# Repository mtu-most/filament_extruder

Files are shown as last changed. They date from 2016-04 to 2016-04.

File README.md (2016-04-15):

<h1>MOST Filament Extruder V4.1</h1>

The MOST filament extruder for making your own filament.

<a href="https://github.com/mtu-most/most-scad-libraries">MOST SCAD libraries</a> are required if the SCAD files are used. Put all SCAD files in the same directory. The renderer provides a relatively easy way to render the parts while still allowing the extruder library to be used in other designs.

Models of all the printed parts are available in the models/stl directory and pictures of the printed parts may be found in models/rendering.

Development of the electronics was done with Kicad and all source is available in the aptly named kicad directory. Gerbers are there, too.

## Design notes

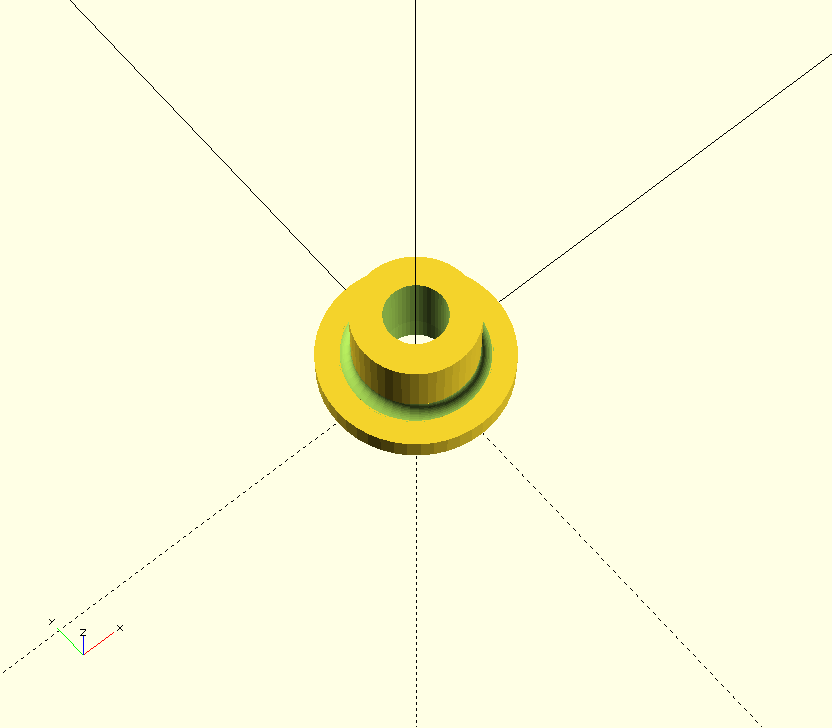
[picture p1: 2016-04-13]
models/rendering/bearing_bushing.png

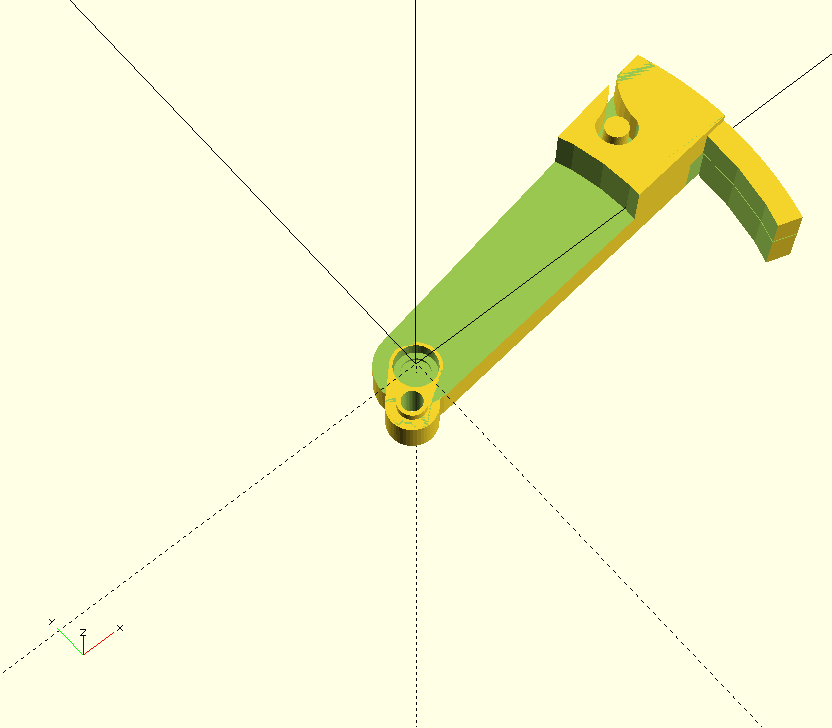
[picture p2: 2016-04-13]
models/rendering/qc_diameter.png

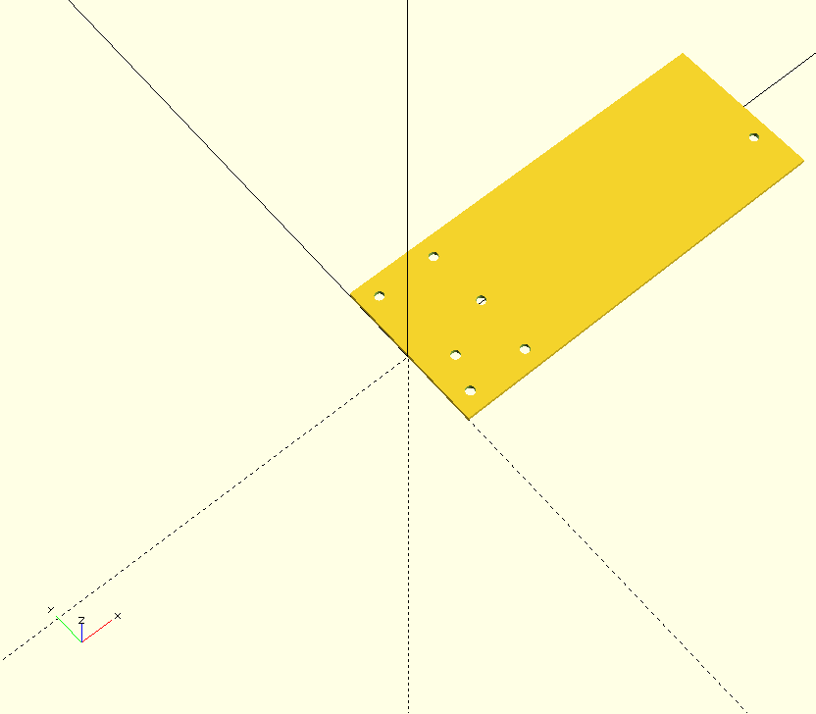
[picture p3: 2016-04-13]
models/rendering/qc_mount-template.png

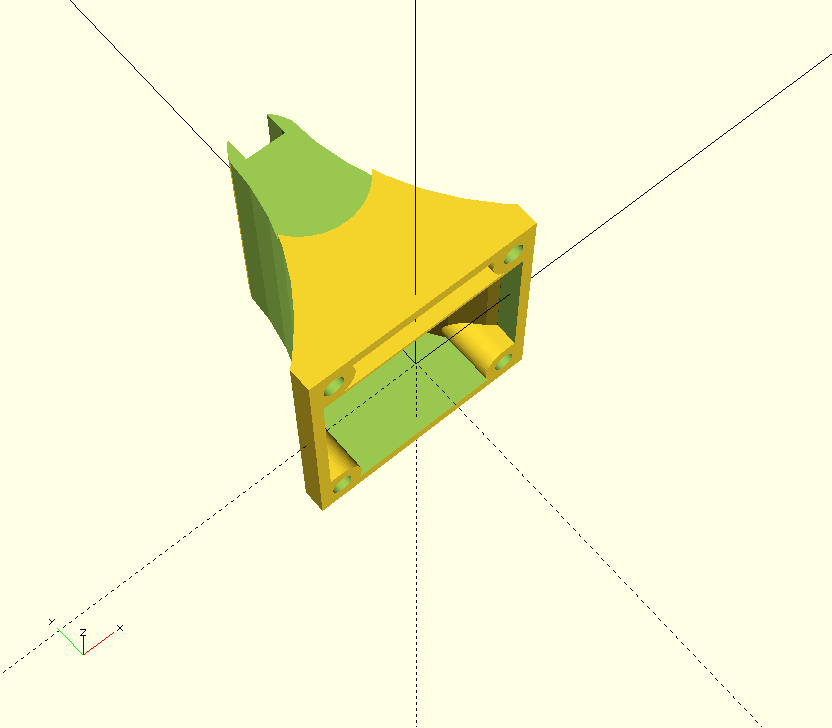
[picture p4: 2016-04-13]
models/rendering/fan_shroud.png

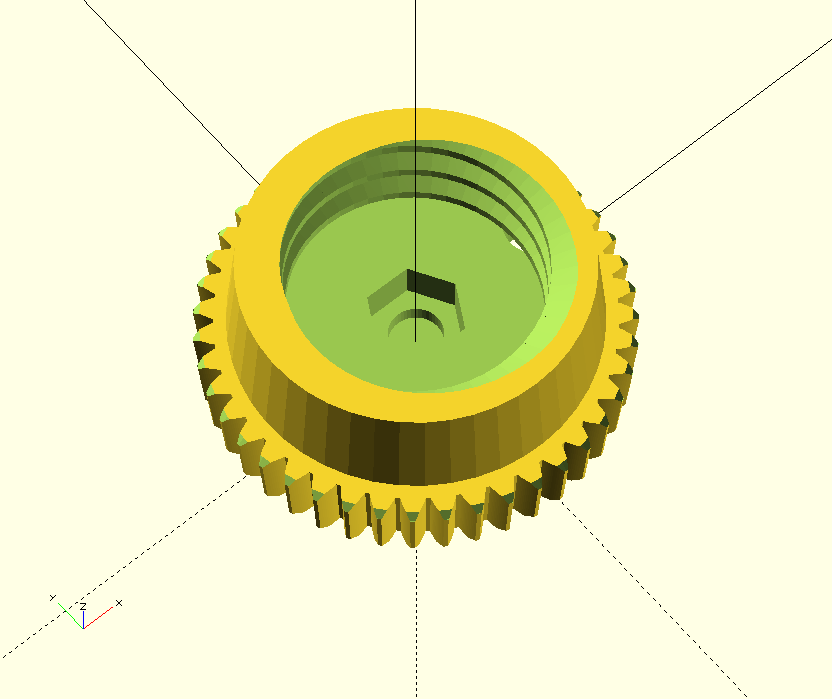
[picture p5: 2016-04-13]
models/rendering/gear_large.png

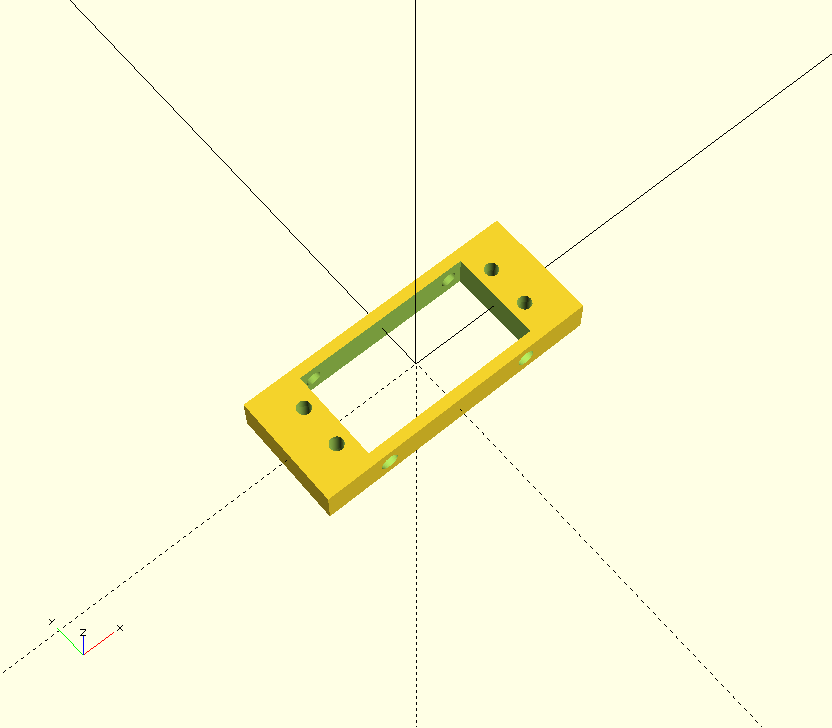
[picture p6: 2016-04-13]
models/rendering/servo_mount.png

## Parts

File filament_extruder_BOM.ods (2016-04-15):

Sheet: Extruder
Filament extruder Bill of Materials
Extruder
Part | Length | Count | Functional group | Description |  | Note | Example
1-5/8” slotted hole strut channel | 24” | 2 | Extruder | Frame base |  |  | http://www.mcmaster.com/#3310t475/=wjtfif
1-1/2” x 2-1/2” x 1/4” angle | 4” | 3 | Extruder | Motor and extruder brackets |  |  | http://www.mcmaster.com/#9017k79/=wjtg2r
5/8” ship auger, 17-18” long |  | 1 | Extruder | Extruder auger |  |  | http://www.mcmaster.com/#2818a12/=wjudd1
1/2” npt brass medium pressure cap with 1.5-2mm hole |  | 1 | Extruder | Extruder nozzle |  |  | http://www.mcmaster.com/#50785k164/=wjug3t
1/4” - 20 threaded rod | 3” | 4 | Extruder | Fixing floor flanges to brackets |  |  | http://www.mcmaster.com/#98841a029/=wjun2h
1/4” - 20 threaded rod | 9” | 2 | Extruder | Fixing all three floor flanges together |  |  | hardware store
1/2” npt black iron floor flange |  | 3 | Extruder | Thermal and torque breaks |  |  | http://www.amazon.com/LDR-310-F-12-Flange-2-Inch/dp/B000FPASJ8
1/2” npt nipple, threaded both ends | 6” | 2 | Extruder | Extruder barrel, feed barrel |  |  | http://www.mcmaster.com/#44615k484/=wjulv6
1/4” - 20 nuts |  | 20 | Extruder | various |  |  | http://www.mcmaster.com/#90473a029/=wjuout
1/4” washers |  | 24 | Extruder | various |  |  | http://www.mcmaster.com/#92141a029/=wjuplf
¼' – 20 7/8” OD fender washers |  | 4 | Extruder | Thrust bearing retainers |  |  | http://www.mcmaster.com/#91090a107/=wjur3k
1” wheel bearing |  | 1 | Extruder | Thrust bearing |  | Bearing block may need to be modified depending on OD or outer race | http://www.amazon.com/Martin-Wheel-BK-1-Bearing-Repair/dp/B00C1ZQT6G?s=automotive
Kapton tape |  |  | Extruder | Fixing nichrome to barrel
1/2” fiberglass pipe insulation | 5” | 1 | Extruder | Hot end insulator |  |  | http://www.mcmaster.com/#5556k31/=ww86uo
Printed bearing block |  | 1 | Extruder | Thrust bearing block
Printed feed chute front |  | 1 | Extruder | Feed chute
Printed feed chute back |  | 1 | Extruder | Feed chute
M3 x 16mm socket head cap screw |  | 4 | Extruder | Feed chute
1/4” - 20 strut channel nut |  | 6 | Extruder | Fixing angle brackets to strut |  |  | http://www.mcmaster.com/#3259t31/=z2wsyp
1/4” - 20 strut channel nut |  | 2 | Extruder | Fixing hanger bracket to strut |  |  | http://www.mcmaster.com/#3259t31/=z2wsyp
Hanger bracket |  | 1 | Extruder | Hanging extruder |  | manufactured
4cm x 4cm 1 1cm 24VDC fan |  | 1 | Extruder | Cooling fan
Printed fan mount |  | 1 | Extruder | Cooling fan mount
M3 x 35mm socket head cap screw |  | 4 | Extruder | Cooling fan mount
M3 hex nut |  | 4 | Extruder | Cooling fan mount
Printed cooling fan shroud |  | 1 | Extruder | Cooling fan mount
3mm id x 6mm OD PTFE tubing | 18” | 1 | Extruder | Filament guide sheathing
AC-powered version
22 rpm AC gear motor, 110V w/speed control, bracket and mounting screws |  | 1 | Extruder | Extruder drive motor |  |  | http://www.amazon.com/21rpm-Factory-Motor-Controller-Bracket/dp/B00G34C37A?s=lamps-light
15mm rigid shaft coupling w/ keyway |  | 1 | Extruder | Gearbox-auger coupling |  |  | http://www.mcmaster.com/#5395t512/=wjtj2m
7/16” deep socket, 1/4” drive |  | 1 | Extruder | Gearbox-auger coupling |  |  | http://www.mcmaster.com/#5543a76/=wjucze
31AWG glass insulated Nichrome wire, 8 ohm/ft | 17' | 1 | Extruder | Extruder barrel heating element |  |  | https://ultimachine.com/content/31-awg-nichrome-wire-0 | 31AWG glass insulated Nichrome wire, 8 ohm/ft | 31AWG glass insulated Nichrome wire, 8 ohm/ft | 17 | 1 | Extruder barrel heating element | https://ultimachine.com/content/31-awg-nichrome-wire-0 | 31AWG glass insulated Nichrome wire, 8 ohm/ft | 17 | 1 | Extruder barrel heating element | https://ultimachine.com/content/31-awg-nichrome-wire-0 | 31AWG glass insulated Nichrome wire, 8 ohm/ft | 17 | 1 | Extruder barrel heating element | https://ultimachine.com/content/31-awg-nichrome-wire-0 | 31AWG glass insulated Nichrome wire, 8 ohm/ft | 17 | 1 | Extruder barrel heating element | https://ultimachine.com/content/31-awg-nichrome-wire-0 | 31AWG glass insulated Nichrome wire, 8 ohm/ft | 17 | 1 | Extruder barrel heating element | https://ultimachine.com/content/31-awg-nichrome-wire-0 | 31AWG glass insulated Nichrome wire, 8 ohm/ft | 17 | 1
24V, 1A power supply |  | 1 | Extruder | Controller and winder power
DC-powered version
20-25rpm, 120W 24VDC gear motor |  | 1 | Extruder | Extruder drive motor |  |  | http://www.aliexpress.com/item/5D120GN-C-DC-Permanent-Magnet-Reducer-Gear-Motor-Big-Power-Reverse-Motor-120W-12V-24V/32283520834.html
12mm rigid shaft coupling w/ keyway one side bored to 13mm |  | 1 | Extruder | Gearbox-auger coupling |  |  | http://www.mcmaster.com/#5395t412/=ww8e8e
31AWG glass insulated Nichrome wire, 8 ohm/ft | 3' | 4 | Extruder | Extruder barrel heating element |  | Four lengths total with pairs in parallel and alternating polarity. Total ~96W. | https://ultimachine.com/content/31-awg-nichrome-wire-0
24V, >=5A power supply |  | 1 | Extruder | System power
Controller
LCD w/ I2C communication |  | 1 | Controller | Interface
8 step rotary encoder with switch |  | 1 | Controller | Interface
Printed interface mount |  | 1 | Controller | Interface
MOST Extruder Controller Board |  | 1 | Controller | Controller
Printed controller board mount |  | 1 | Controller | Controller
Printed knob for encoder |  | 1 | Controller | Controller
Four conductor ribbon cable with 4 pin housings each end | 12” | 1 | Controller | LCD wire
3 ea 28ga stranded, insulated wire, 3 pin housing one end | 12” | 1 | Controller | Encoder wire
100k-ohm, radial lead NTP thermistor |  | 1 | Controller | Extruder barrel temp sensor |  |  | http://www.amazon.com/MAX6675-Module-Thermocouple-Sensor-Arduino/dp/B00MPEUVSK?s=industrial
1” hose clamp |  | 1 | Controller | Affixing thermistor to nozzle
Drop Position Sensor
MOST drop position sensor board |  | 1 | Drop position sensor | Drop position sensor
Printed drop position sensor mount |  | 1 | Drop position sensor | Drop position sensor
6-conductor ribbon cable with keyed pin housings each end | 24” | 1 | Drop position sensor | Communication cable to controller
3mm red LED |  | 1 | Drop position sensor | Illuminator
2 ea 28ga stranded, insulated wire, 2 pin housing one end | 8” | 1 | Drop position sensor | LED power wire
Diffuser (matte finish Scotch tape) |  | 1 | Drop position sensor | Drop position sensor
Winder
24V, 24rpm gear motor |  | 1 | Filament winder | Winder drive motor
Printed large gear/spool cone |  | 1 | Filament winder | Winder drive
Printed spool retainer screw |  | 1 | Filament winder | Secure spool to winder
608zz bearing |  | 2 | Filament winder | Winder bearings
M8 x 40mm hex head cap screw |  | 1 | Filament winder | Winder shaft
8mm flat washer |  | 1 | Filament winder | Winder shaft
M8 nylock nut |  | 1 | Filament winder | Winder shaft
Printed spool winder bearing flange |  | 2 | Filament winder | Winder shaft
1/8” x 2” aluminum strap | 6” | 1 | Filament winder | Winder motor mount
Printed small gear |  | 1 | Filament winder | Winder drive
M3 x 8 set screw |  | 1 | Filament winder | Small gear set screw
M3 x 10 socket head cap screw |  | 2 | Filament winder | Secure winder motor mount to frame
3MM flat washer |  | 2 | Filament winder | Secure winder motor mount to frame
Hall effect switch |  | 1 | Filament winder | Winder rotation detector
Cylindrical magnet |  | 1 | Filament winder | Winder rotation detector
Servo |  | 1 | Filament winder | Winder positioner
Printed filament positioner arm |  | 1 | Filament winder | Winder positioner
Printed servo mount |  | 1 | Filament winder | Winder positioner
M3 x 30 countersunk socket screw |  | 2 | Filament winder | Winder positioner mounting
M3 hex nut |  | 4 | Filament winder | Winder positioner mounting
M3 x 10 socket head cap screw |  | 4 | Filament winder | Servo mounting
M3 hex nut |  | 4 | Filament winder | Servo mounting
3mm flat washer |  | 4 | Filament winder | Servo mounting
3mm id x 6mm OD PTFE tubing | 1/4” | 1 | Filament winder | Low friction filament path for positioner
Diameter and length measurement
1/8” x 2” aluminum strap | 7” | 1 | Length & Diameter | Mounting bracket
Printed diameter lever |  | 1 | Diameter Measurement | Diameter measurement
MR105zz bearing |  | 6 | Diameter Measurement | 2 Lever bearings, 4 filament gauge bearings
M5 x 16 socket head cap screw |  | 1 | Diameter Measurement | lever gauge bearing shaft
M5 x 40 fully threaded socket head cap screw |  | 1 | Diameter Measurement | Idler gauge bearing shaft
M5 x 20 socket head cap screw |  | 1 | Diameter Measurement | Diameter lever pivot shaft
5mm flat washer x 8mm od |  | 1 | Diameter Measurement | Washer on mount side of diameter lever pivot | Produced by chucking an M5 screw with a 5mm washer and nut on it in a drill and turning down with a file.
GT2 belt | 12” | 1 | Diameter Measurement | Diameter measurement pulley engagement
16 tooth GT2 pulley bored to 6.4mm |  | 1 | Diameter Measurement | Diameter measurement pulley engagement
Bourns PDB241-GTR02-104BO linear taper, low friction potentiometer |  | 1 | Diameter Measurement | Signal producing device for diameter measurement
M3 grub screw |  | 1 | Diameter Measurement | Affixing GT2 pulley to pot
Weight |  | 1 | Diameter Measurement | Belt tensioner
Printed filament guide |  | 1 | Diameter Measurement | Guides filament through diameter measurement device
M5 hex nut |  | 1 | Diameter Measurement | Idler bearing shaft nut
Printed length measurement device mount |  | 1 | Length Measurement
Printed length measurement rotor |  | 1 | Length Measurement
Cylinder magnet |  | 1 | Length Measurement
M5 x 20 hex head cap screw |  | 1 | Length Measurement | Rotor shaft
mk7 filament drive gear and set screw |  | 1 | Length Measurement
5mm flat washer |  | 2-4 | Length Measurement | Shims for drive gear
625zz bearing |  | 2 | Length Measurement | Rotor shaft bearings
Hall effect switch |  | 1 | Length Measurement | Rotation detector

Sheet: Winder
Part | Length | Count | Description | Note | Example
Servo |  | 1 | Filament winder guide |  | https://www.adafruit.com/products/155
FilaWinder electronics kit |  | 1 | Controller, sensor, cable | This needs to be replaced with something better | http://www.filastruder.com/products/filawinder
Momentary contact push button switch |  | 3 | Controller interface
5k-ohm potentiomer |  | 1 | Controller interface
SPST rocker switch |  | 2 | Controller interface
2 pin headers |  | 6
3 pin headers |  | 2
Female crimp ends
2” x 1/8” aluminum strip | 6” | 1 | Spool winder mount
608zz bearing |  | 2 | Spool winder shaft
M8 hex head cap screw | 30mm | 1 | Spool winder shaft
M8 nut |  | 1 | Spool winder shaft
Printed bearing blocks |  | 2 | Spool winder shaft
Printed spool gear (large) |  | 1 | Spool winder drive
Printed small gear |  | 1 | Spool winder drive
M3 nut |  | 1 | Set screw for small gear
M3 x 6mm set screw |  | 1 | Set screw for small gear
M3 x 6mm socket head cap screw |  | 1 | Spool winder drive motor mount
6mm diameter Nd magnet |  | 1 | Spool winder rotation detector
Printed filament guide arm |  | 1 | Spacing coil on spool
M3 x 12mm socket head cap screw |  | 2 | Filament guide servo mount
M3 washer |  | 2 | Filament guide servo mount
Printed servo mount |  | 1 | Filament guide servo mount
M3 x 25mm flat-head socket cap screw |  | 2 | Filament guide servo mount
M3 nut |  | 2 | Filament guide servo mount
M3 washer |  | 2 | Filament guide servo mount
Printed control panel |  | 1 | For interface
Printed sensor mount |  | 1 | Filament drop sensor
Printed sensor shroud |  | 1 | Filament drop sensor
Printed fan mount |  | 1 | Filament cooling
Printed fan shroud |  | 1 | Filament cooling
40mm box fan |  | 1 | Filament cooling
1/4” - 20 threaded rod | 36” | 2 | Sensor and fan mounting
1/4” - 20 nut |  | 8 | Sensor and fan mounting
1/4” washer |  | 4 | Sensor and fan mounting
Printed threaded rod mounts |  | 2 | Sensor and fan mounting
1/2” - 13 nut |  | 2 | Sensor and fan mounting
1/2” washer |  | 2 | Sensor and fan mounting
PTFE tubing | 10mm | 1 | Fan filament guide
M3 x 25mm socket head cap screws |  | 4 | Fan mount
M3 nut |  | 4 | Fan mount
M3 washer |  | 4 | Fan mount
LED |  | 1 | Filament drop sensor
Linear sensor array |  | 1 | Filament drop sensor |  | http://www.digikey.com/product-detail/en/TSL1406R/TSL1406-R-ND/3095064
Linear sensor PCB |  | 1 | Filament drop sensor | custom
Printed control board mount |  | 1
M3 x 10mm socket head cap screw |  | 2 | Control board mount
M3 x 6mm socket head cap screw |  | 2 | Control board mount
M3 x 10mm socket head cap screw |  | 2 | Spool winder mount
M3 washer |  | 2 | Spool winder mount
Connection wire |  |  | Various
AC-powered version
12VDC 30 rpm gear motor |  | 1 | Spool winder drive |  | http://www.aliexpress.com/item/24V-6mm-Diameter-Shaft-2-Pins-Terminal-30RPM-Gearbox-DC-Gear-Motor/32238311086.html
DC-powered version
24VDC 30 rpm gear motor |  | 1 | Spool winder drive |  | http://www.aliexpress.com/item/JL-37B3540-216-2430-Electric-Replacing-DC24V-30RPM-DC-Gear-Motor/32323787933.html

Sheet: QC
Part | Length | Count | Description | Note | Example
2” x 1/8” aluminum strip | 7” | 1 | Mount
Low torque potentiometer |  | 1 | Diameter measurement
Rotary encoder |  | 1 | Length measurement
M5 x 25mm hex head cap screw |  | 1 | Idler roller shaft
M5 nut |  | 3 | Idler roller shaft
M5 nut |  | 1 | Pressor roller
MR105zz ball bearing |  | 2 | Pressor and idler rollers
MR105zz ball bearing |  | 2 | Lever bearings
M5 X 20mm socket head cap screw |  | 1 | Lever shaft
M5 nut |  | 1 | Lever shaft
16 tooth GT2 pulley w/ set screw |  | 1 | Diameter measurement
GT2 belt | 40cm | 1 | Diameter measurement
Printed encoder mount |  | 1
Printed lever |  | 1
Printed filament guide |  | 1
PTFE tubing | 25mm | 1 | Diameter-to-length
PTFE tubing | 10mm | 1 | Diameter outlet
PTFE tubing | 40mm | 1 | Length inlet
Connection wire |  |  | Various
2 x 16 LCD panel |  | 1 | Interface
LCD I2C backpack |  | 1 | Interface | Required since insufficient number of pins available on Arduino

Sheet: electronics
Function | Count | Spec/Similar | Price
Controller | 1 | AVR (version?)
Heater power switching | 1 | high power FET (STM STP55NF06) | 1.11
Spool winder motor power switching | 1 | low power FET (STM STP55NF06) | 1.11
Rotary encoder with switch | 1 | (Bourns PEC12R-4120F-S0012) | 1.21
1602 LCD Panel w/ I2C adapter | 1 | (see aliexpress.com) | 1.96
Length measurement | 1 | 400 step low torque rotary encoder (see aliexpress.com) | 12.19
Diameter measurement | 1 | low torque linear taper potentiometer (Bourns series....)
Spool winder motor | 1 | 24V DC gearmotor (see aliexpress.com) | 15.33
Spool rotation sensor | 1 | Hall effect sensor (Optek OH090U) | 1.67
Auger rotation sensor | 1 | Hall effect sensor (Optek OH090U) | 1.67
Drop sensor | 1 | Linear sensor array, TSL1406R (see mouser.com) | 23.93
Drop sensor illumination | 1 | LED, red (see any) | 0.2
Drop sensor controller | 1 | ATTINY45-20XUR (see digikey.com) | 1.42
Hot end temperature sensor | 1 | AD8495 (see digikey.com) | 4.81
Hot end temperature thermocouple | 1 | Type k thermocouple (see amazon.com) | 1.15
Main controller board | 1 | Custom
Drop sensor board | 1 | Custom
Thermocouple amplifier board | 1 | Custom
Not electronic:
Spool rotation sensor magnet | 1 | 3/16” X 1/4” Nd magnet (see K&J magnetics) | 0.38
Auger rotation sensor magnet | 1 | 3/16” X 1/4” Nd magnet (see K&J magnetics) | 0.38
Diameter measurement sensor pulley | 1 | 16 tooth GT2 pulley (see robotdigg.com) | 1.8
Diameter measurement idler bearing | 1 | MR105zz (see robotdigg.com) | 0.6
Diameter measurement idler flanged bearing | 1 | MF105zz (see amazon.com) | 1.19
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

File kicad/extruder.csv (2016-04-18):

Id | Designator | Package | Quantity | Designation | Supplier and ref
1 | C1,C2 | C_0805 | 2 | C22pF
2 | R3,R2,R1 | R_0603 | 3 | R100k
3 | Y1 | Crystal_HC49-SD_SMD | 1 | Crystal
4 | cpu1 | TQFP-32_7x7mm_Pitch0.8mm | 1 | ATMEGA328P-A
5 | ctemp1 | c_elec_3x5.3 | 1 | CP10uF
6 | P1 | Pin_Header_Straight_1x02 | 1 | therm
7 | P2 | Pin_Header_Straight_1x04 | 1 | lcd
8 | P4 | Pin_Header_Straight_1x04 | 1 | qc
9 | P5 | Pin_Header_Straight_1x06 | 1 | ftdi
10 | P6 | Pin_Header_Straight_1x03 | 1 | servo
11 | P7 | Pin_Header_Straight_1x03 | 1 | hall
12 | P11 | Pin_Header_Straight_1x04 | 1 | enc
13 | P12 | Pin_Header_Straight_2x03 | 1 | icsp
14 | Q1,Q2,Q3 | TO-252-2Lead | 3 | IRLR2905PBF
15 | rtemp1 | R_1206 | 1 | R4.7k
16 | P8 | 2Screw | 1 | htr
17 | P13 | 2Screw | 1 | pwr
18 | P14 | Pin_Header_Straight_2x03 | 1 | 24V
19 | P15 | Pin_Header_Straight_2x03 | 1 | 5V
20 | PSU1 | 7-28V | 1 | DC-DC_Buck
21 | D1,D2,D3 | DO-214AC | 3 | D
22 | P9 | Pin_Header_Straight_1x02 | 1 | winder
23 | P10 | 2Screw | 1 | auger
24 | P3,P16,P17,P18 | 1pin | 4 | CONN_01X01
25 | W1,W3,W4 | Pin_Header_Straight_1x01 | 3 | TEST_1P

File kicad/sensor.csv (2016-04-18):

Id | Designator | Package | Quantity | Designation | Supplier and ref
1 | RV1 | Potentiometer_Trimmer-Bourne_TC33-X2 | 1 | POT
2 | O1 | TSL1406R | 1 | TSL1406R
3 | IC1 | SOIJ-8_5.3x5.3mm_Pitch1.27mm | 1 | ATTINY45-S
4 | P1 | Pin_Header_Angled_2x03 | 1 | ICSP
5 | P2 | Pin_Header_Angled_1x02 | 1 | LED
6 | R1 | R_1206 | 1 | R100

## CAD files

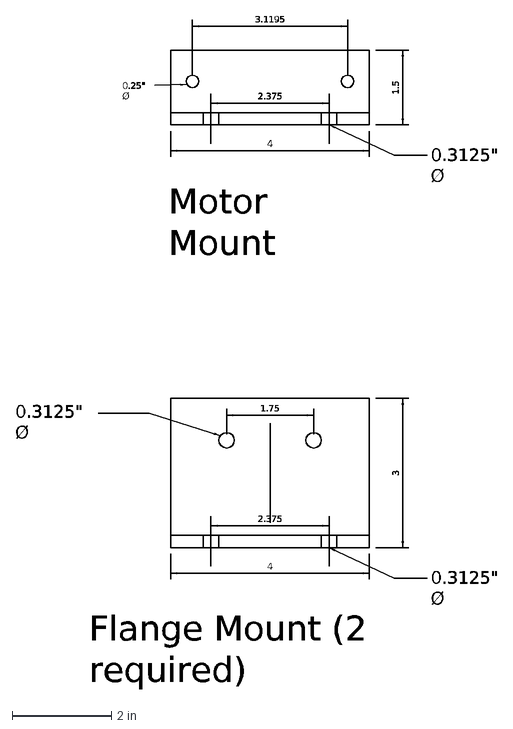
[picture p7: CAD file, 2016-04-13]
cad/motor and flange mounts.dxf
2.375
0.3125" Ø
4
3
1.75
Flange Mount (2 required)
3.1195
0.25" Ø
1.5
Motor Mount

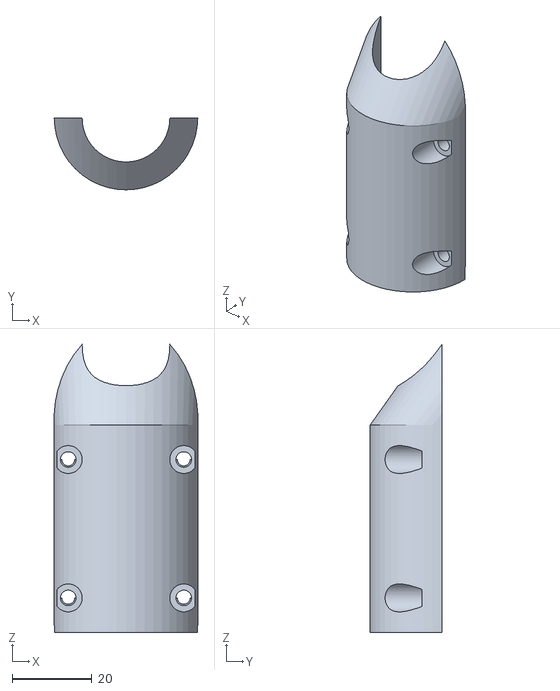
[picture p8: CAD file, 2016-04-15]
models/stl/feed_chute_back.stl
36.1 x 18.0 x 72.3

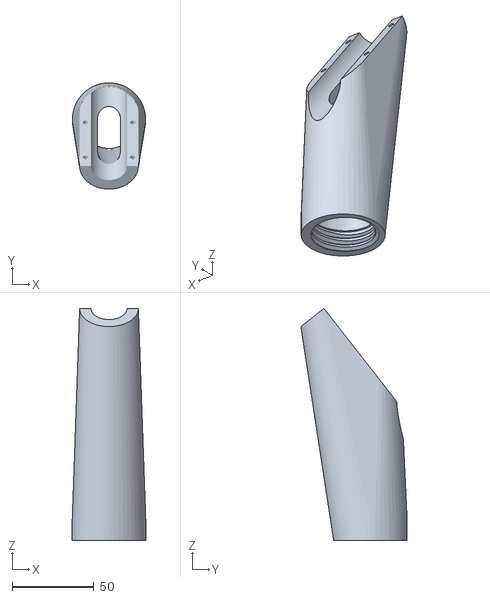
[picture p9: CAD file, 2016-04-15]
models/stl/feed_chute_front.stl
45.0 x 65.1 x 142.0

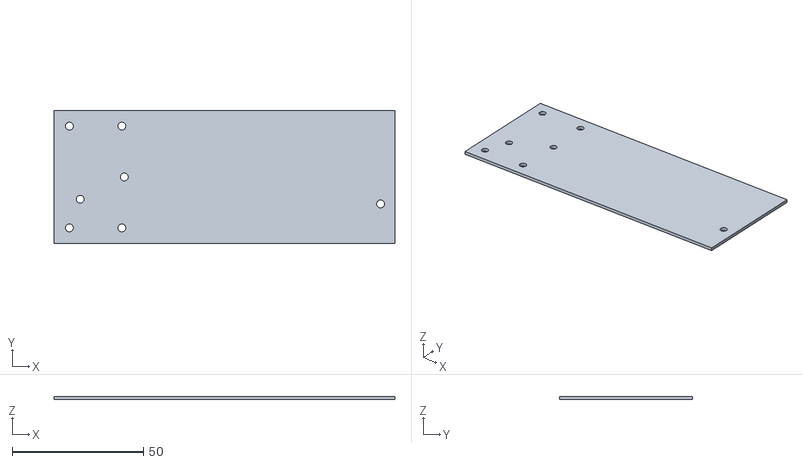
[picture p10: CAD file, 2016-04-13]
models/stl/qc_mount_template.stl
130.0 x 50.8 x 1.33

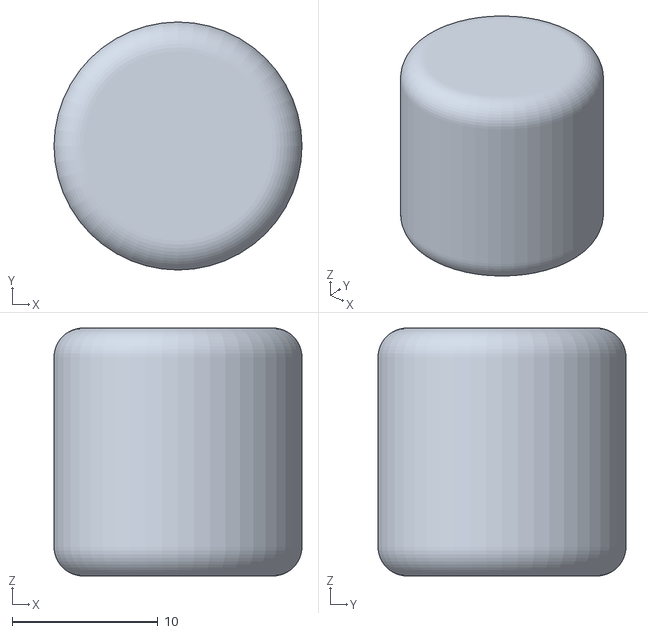
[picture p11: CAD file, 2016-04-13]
models/stl/encoder_knob.stl
17.0 x 17.0 x 17.0

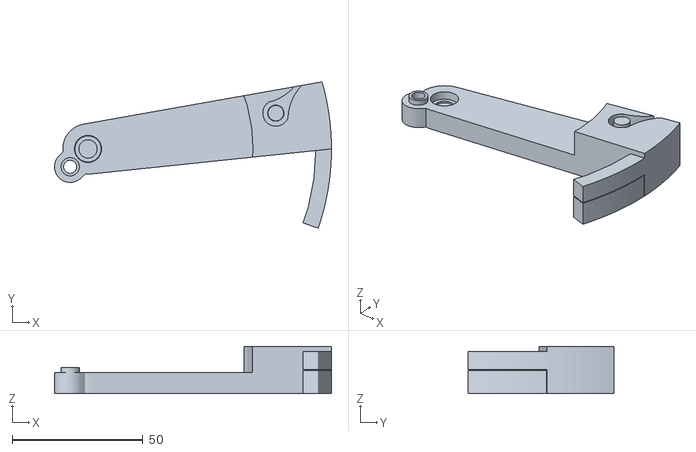
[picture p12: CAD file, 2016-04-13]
models/stl/qc_diameter.stl
105.9 x 56.0 x 18.0

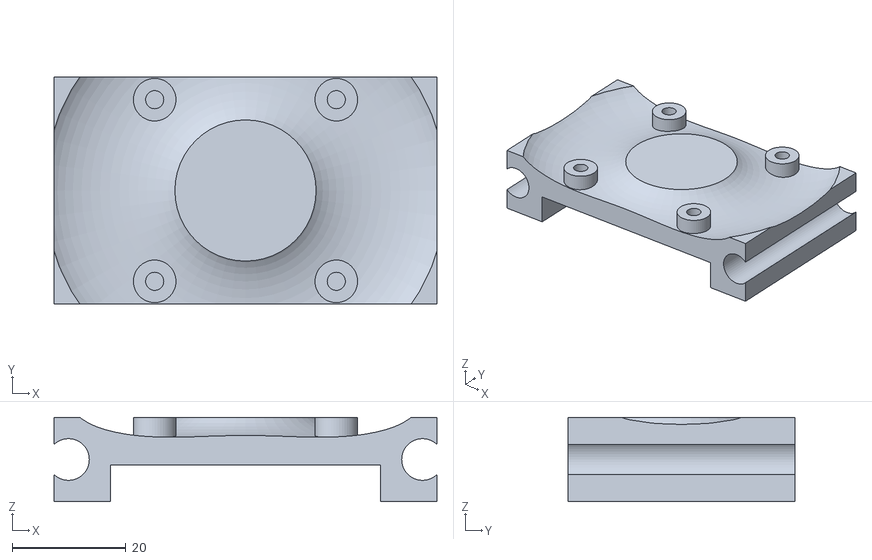
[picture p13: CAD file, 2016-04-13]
models/stl/fan_mount.stl
67.5 x 40.0 x 14.8

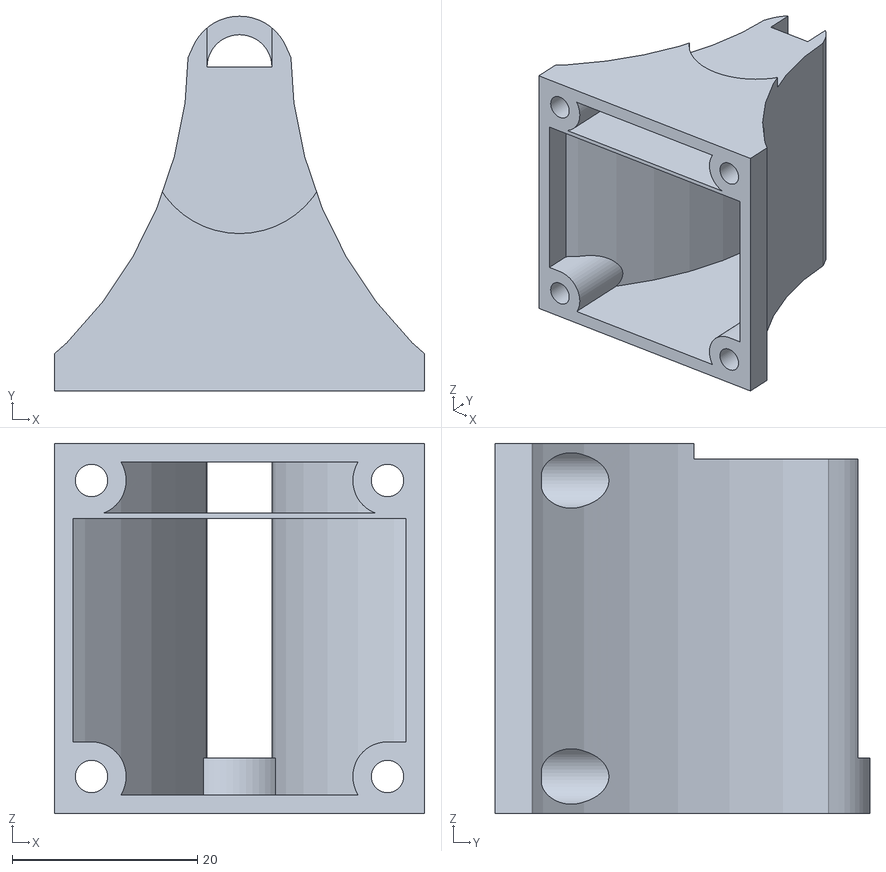
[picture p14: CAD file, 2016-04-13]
models/stl/fan_shroud.stl
40.0 x 40.5 x 40.0

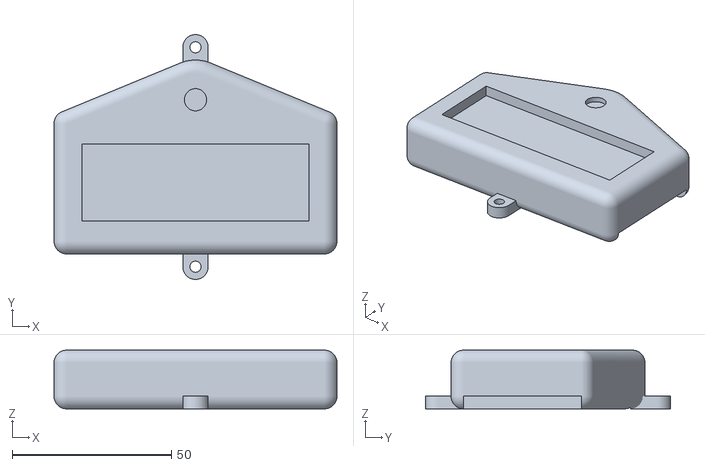
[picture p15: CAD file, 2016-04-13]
models/stl/display_mount.stl
89.0 x 77.0 x 18.5

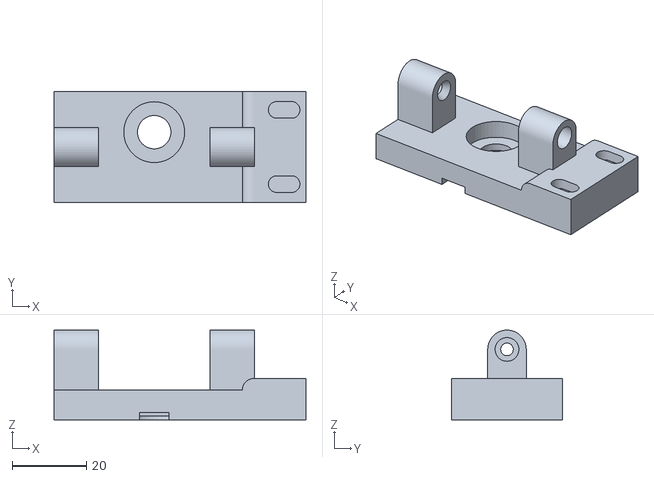
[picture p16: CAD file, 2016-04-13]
models/stl/qc_length.stl
67.9 x 30.0 x 24.2

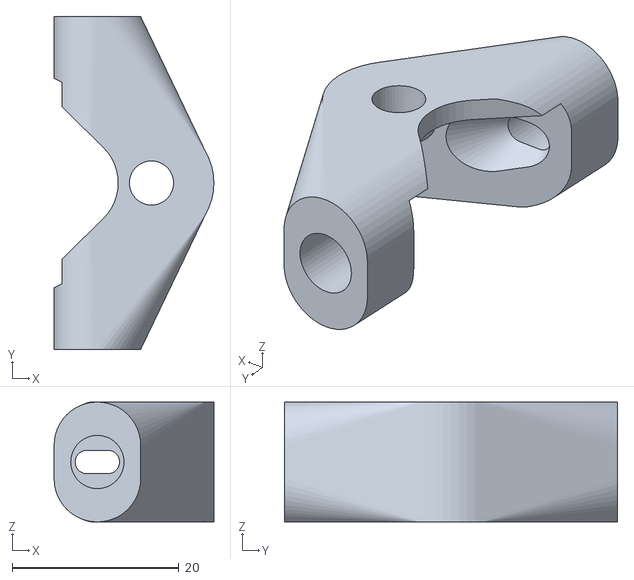
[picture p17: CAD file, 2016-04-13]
models/stl/filament_guide.stl
19.2 x 40.0 x 14.4

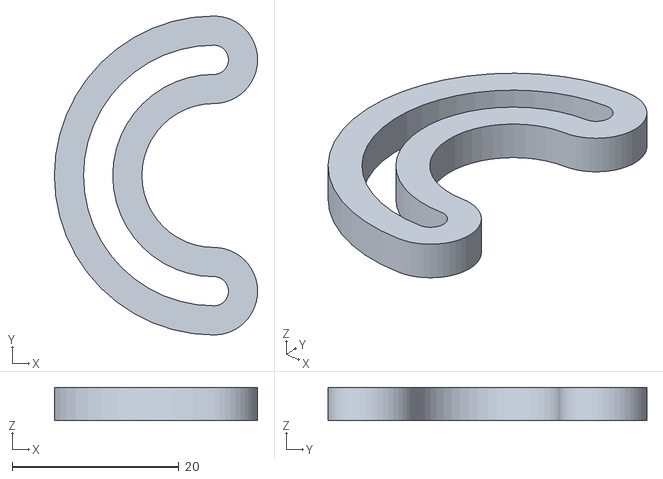
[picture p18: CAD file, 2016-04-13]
models/stl/winder_motor_stay.stl
24.4 x 38.2 x 4.00

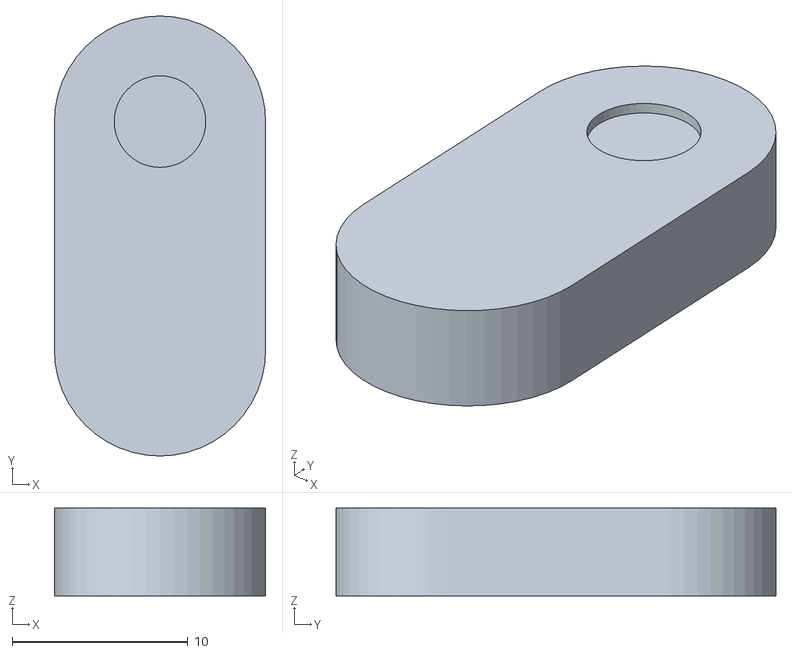
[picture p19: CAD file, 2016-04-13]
models/stl/qc_length_rotor.stl
12.0 x 25.0 x 5.00

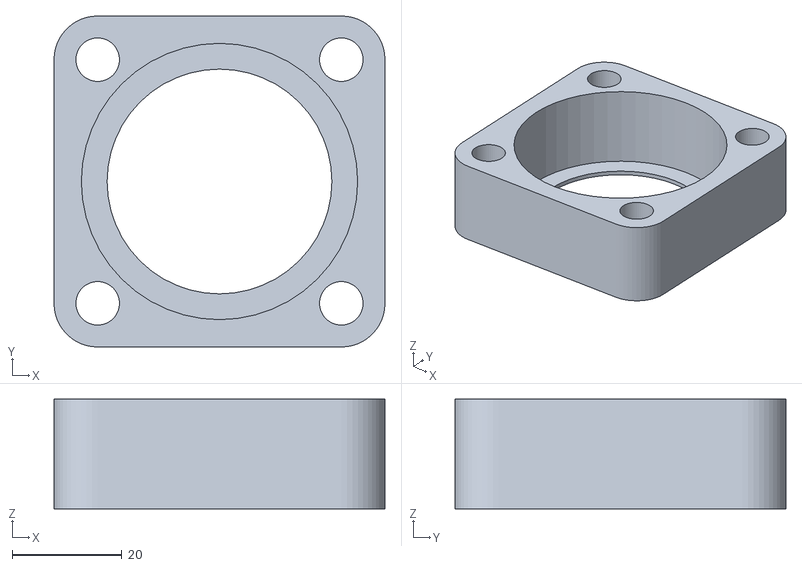
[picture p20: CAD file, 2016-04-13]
models/stl/trailer_bearing_block.stl
60.4 x 60.4 x 20.0

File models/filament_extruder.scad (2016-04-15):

/************************************************************************************

filament_winder.scad - various parts for the winder portion of the MOST filament extruder V10000
Copyright 2015 Jerry Anzalone
Author: Jerry Anzalone <gcanzalo@mtu.edu>

This program is free software: you can redistribute it and/or modify
it under the terms of the GNU Affero General Public License as
published by the Free Software Foundation, either version 3 of the
License, or (at your option) any later version.

This program is distributed in the hope that it will be useful,
but WITHOUT ANY WARRANTY; without even the implied warranty of
MERCHANTABILITY or FITNESS FOR A PARTICULAR PURPOSE. See the
GNU Affero General Public License for more details.

You should have received a copy of the GNU Affero General Public License
along with this program. If not, see <http://www.gnu.org/licenses/>.

************************************************************************************/

include<bearings.scad>
include<fasteners.scad>
include<threads.scad>
include<gear_calculator.scad>
include<parametric_involute_gear_v5.0.scad>

$fn = 48;

layer_height = 0.3;

pi = 3.14159265359;

// extruder parts
od_pipe = 22; // measured 21.52
l_gap = 10;
h_gap = 1.5 * 25.4;
pad_pipe = 7;
od_pipe_engagement = od_pipe + 2 * pad_pipe;
h_pipe_engagement = h_gap + 2 * pad_pipe;
od_hopper_engagement = 24;
l_hopper_base = 70;
w_hopper_base = 25;
t_hopper_walls = 4;
w_clamp = od_pipe_engagement / 2 + 8;
l_clamp = 8;
y_offset_hopper = 45 + od_hopper_engagement / 2;
z_offset_hopper = 80;

cc_flange_mounts = 7 * 25.4 / 4;
d_flange_mounts = 5 * 25.4 / 16;
h_outer_race = 20;
d_outer_race = 50.4;
d_inner = 41;

pitch_hopper = 4.00;
d_hopper = 39; //36.5;
// for the jug adapter:
a_hopper = 38;
pad_threads = 3;
h_threads = 13.1;
id_throat = 30;

h_bushing = 20;
h_bushing_flange = 5;
id_bearing = 25.35;
od_bearing_flange = 39.8;
r_id_bearing = 2.5; // the inner race has a radiused shoulder
d_auger_shank = 12.7;
dmax_auger_shank = 13.25;
h_auger_taper = 6;

// winder motor dims
d_motor_mount_circle = 27.75;
d_motor_mount = 37;
d_shaft_collar = 12;
d_shaft = 6;
d_shaft_flat = 5.3;
l_shaft = 12;
n_mounts = 4;
d_mounts = d_M3_screw;
offset_shaft = 6.81;
t_motor_mount = 4;

// pulleys were originally both 40mm in diameter, changes should be done to both diameters
// to keep belt length the same (unless a different belt is used)
d_pulley_motor = 15;
d_pulley_spool = 65;
d_belt = 4; // belt will be a large o-ring
t_pulley = 6;

id_spool = 52.26;
d_large_cone = id_spool + 2.5;
d_small_cone = id_spool - 2.5;
h_cone = 15;

d_cone_shaft = 8;

d_magnet = 10;// 6.3;
h_magnet = 3;//6.3;

d_c_rod = 5; // using carbon fiber rod for the spool holder since it's available
d_frame_mount = d_M3_screw; // screw diameter mounting dpool holder to frame
offset_frame_mount = 10;
h_frame_mount = offset_frame_mount + d_frame_mount + 3;

bearing_idler = bearing_608;

// servo dims
w_servo = 20;
l_servo = 40.2;
l_servo_flange = 55;
cc_w_servo_mounts = 10;
cc_l_servo_mounts = 48;
d_servo_mounts = d_M3_screw;

d_cable = 7;
d_cable_holder = d_cable + 2;

l_strut_slot = 28; // measure 28.32
d_strut_slot = 14; // measured 14.32
cc_strut_slots = 62.4;

d_sensor_threaded_rod = 25.4 / 4 + 0.5; // diameter of threaded rod holding the sensor and goodies

// light sensor board dims - origin is corner nearest screw terminal
l_sensor_board = 80;
w_sensor_board = 25;
l_sensor = 61.48; // tsl1406r - 61.33
w_sensor = 13.1; // tsl1406r - 12.95
t_sensor = 3.3;
pad_sensor = 3; // sides of sensor surrounded by this much plastic
t_sensor_mount = 10; // the light-facing side of the sensor will have this much plastic over it
cc_sensor_mounts = 2.25 * 25.4;
offset_sensor_centerline = w_sensor / 2 - 5.435;
d_sensor_mounts = 1.75; // 2.3mm diameter openings in sensor
offset_sensor = 25; // distance from axis of threaded rod to center of sensor
l_slot = 43; // 55.5 microns high x 768 pixels = 42.624mm
w_slot = 0.5; // width of the light slot in the sensor mount
l_light_path = 90;

w_sensor_mount = offset_sensor + w_sensor + 6; // width of the sensor mount
l_sensor_mount = l_sensor + 6;

d_light_source = 3; // diameter of the light source
pad_light_source = 3;
t_light_source_mount = 6;
d_light_source_pinhole = 0.5;

// main board dimensions
l_main_board = 71;
w_main_board = 44;
cc_l_mounts = 67 - 3.25;
cc_w_mounts = 39 - 3.25;

d_guide = 4; // ptfe tubing guides

// tensioner loop:
d_loop_tensioner = 135;
d_tensioner = 7;
tensioner_entry_offset = 100;

// quality control device measures diameter and total length of filament
// filament travels through device parallel the x-axis
qc_bearings = bearing_MR105;			// all bearings are the same for simplicity - MR105z keeps the overall sive of the lever down
qc_advantage = 9.65;								// ratio of long:short. Precision increases with increasing advantage.
d_qc_drive_gear = 12.5;						// diamter of the drive gear body
d_qc_drive_gear_hob = 11.3;				// diameter of the hobbed poriton of drive gear
d_qc_encoder_mount = 7; 					// d_M7_screw;
d_qc_pivot = d_M5_screw;
t_qc_lever = 18;									// end thickness of the lever
t_qc_lever_pivot = 8;
qc_pulley_pitch = 2;
qc_pulley_teeth = 16;
qc_pot_mechanical_rotation = 300;	// maximum rotation of potentiometer
qc_max_displacement = 2.5; 				// maximum diameter of the filament to be measured
qc_target_displacement = 1.75; 		// target displacement
a_qc_bearings = 45;								// the idler will be angle about the pivot with respect to the x-axis by this amount

/* it's easier to calculate displacement from angle subtended:
		theta = 1; // angle resulting from displacement
		f = 2 * qc_short * pow(sin(theta / 2), 2); // short leg of triangle
		e = (qc_bearings[0] + d_qc_drive_gear_hob) / 2 + 2 * qc_short * sin(theta / 2) * cos(theta / 2); // long leg of triangle
		D = pow(pow(e, 2) + pow(f, 2), 0.5) - qc_bearings[0]; // displacement happens on the hypotenuse; subtract bearing radii from h to get D

		Doing this in a spreadsheet, plotting a vs D and fitting a line to the area of interest yields
		a good approximation of angle from D, the method used below
*/

// calculation of the total angle subtended can be approximated linearly up to 5 mm diameter by:
d_qc_pulley = qc_pulley_pitch * qc_pulley_teeth / pi / 2;
a_max_qc = (qc_max_displacement - 0.047763) / 0.153332;
a_target_qc = (qc_target_displacement - 0.047763) / 0.153332;
// short side of pivot determined by the diameter of the idler bearing and diameter of pivot
qc_short = (qc_bearings[0] + d_qc_pivot) / 2 + 2;				// add a bit for an M5 nut on the pivot
qc_long = qc_short * qc_advantage;
max_qc_pot_rotation = 360 * a_max_qc * qc_long * pi / 180 / (qc_pulley_pitch * qc_pulley_teeth);
target_qc_pot_rotation = 360 * a_target_qc * qc_long * pi / 180 / (qc_pulley_pitch * qc_pulley_teeth);

// stationary bearings are offset to keep the filament straight when at target displacement:
x_offset_qc_stationary = qc_short * cos(180 - a_qc_bearings) - qc_bearings[0];
y_offset_qc_stationary = -qc_short * (1 - cos(a_qc_bearings - a_target_qc) + sin(a_qc_bearings));

// length measurement instrument
// encoder will sit between two pieces of PTFE tubing so that the filament must bend over the drive gear
l_filament_path = 30;
deflection = 1.9;
od_tubing = 6.4;		// 3mm id x 6mm od PTFE tubing
id_tubing = 3;
pad_tubing = 2;
l_qc_length_base = l_filament_path + 24;
w_qc_length_base = 30;
t_qc_length_base = 8;
z_offset_tubing = 11; // the bearings on the diameter measurement tool are about 11mm off plate face
offset_encoder = d_qc_drive_gear_hob / 2 + qc_target_displacement / 2 - (id_tubing - qc_target_displacement) / 2 - deflection;
cc_qc_length_mounts = w_qc_length_base - 10;
inset_qc_length_mounts = 6;
d_encoder_mount = 6.8;

// for the qc mounting plate
l_qc_mount = ceil(qc_long - x_offset_qc_stationary + 20);
w_qc_mount = 2 * 25.4;	// 2" x 1/8" Al strip
t_qc_mount = 3;

color_bearing = [0.6, 0.6, 0.6];
color_fastener = [0, 0.7, 0];

w_al_strip = 25.4 * 2;
t_al_strip = 25.4 / 8;
spool_drive_cc = 40; // spool drive gear c-c
n_teeth_small = 13;
n_teeth_large = 44;
t_gear = 12;
pitch_spool_threads = 6;
d_spool_threads = d_small_cone - 6;

cp = fit_spur_gears(n1 = n_teeth_small, n2 = n_teeth_large, spacing = spool_drive_cc);
r_spool_magnet_circle = outer_radius(teeth = n_teeth_large, circular_pitch = cp) - d_magnet / 2 - 4;

d_encoder_knob = 17;

d_fan_blade = 38;
d_fan_hub = 25;
h_fan_mount = d_sensor_threaded_rod + 8;
cc_fan_mounts = 32;
d_fan_shroud_outlet = d_tensioner + 4;
offset_fan_entry = 33;
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

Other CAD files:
models/stl/thread_holder.stl
models/stl/gear_small.stl
models/stl/servo_mount.stl
models/stl/bearing_bushing.stl
models/filament_extruder_renderer.scad
models/stl/feed_chute.stl
models/stl/filament_guide_arm.stl
models/stl/gear_large.stl
models/stl/idler_cone.stl
models/stl/sensor_mount.stl
models/stl/spool_drive_bearing_block.stl

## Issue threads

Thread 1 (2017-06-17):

libraries are lacking

Patola, 2017-06-17:
As per the README, I cloned most-scad-libraries and linked all scad files to the models/ directory; however, filament_extruder.scad and filament_extruder_rendered.scad still complained about the lack of threads.scad library. I found one such library on thingiverse, installed it, ad it almost worked - now it complains about the lack of a specific variable:
WARNING: Ignoring unknown variable 'bearing_MR105'.
...and it doesn't work. Which exact libraries I have to have to make it work?

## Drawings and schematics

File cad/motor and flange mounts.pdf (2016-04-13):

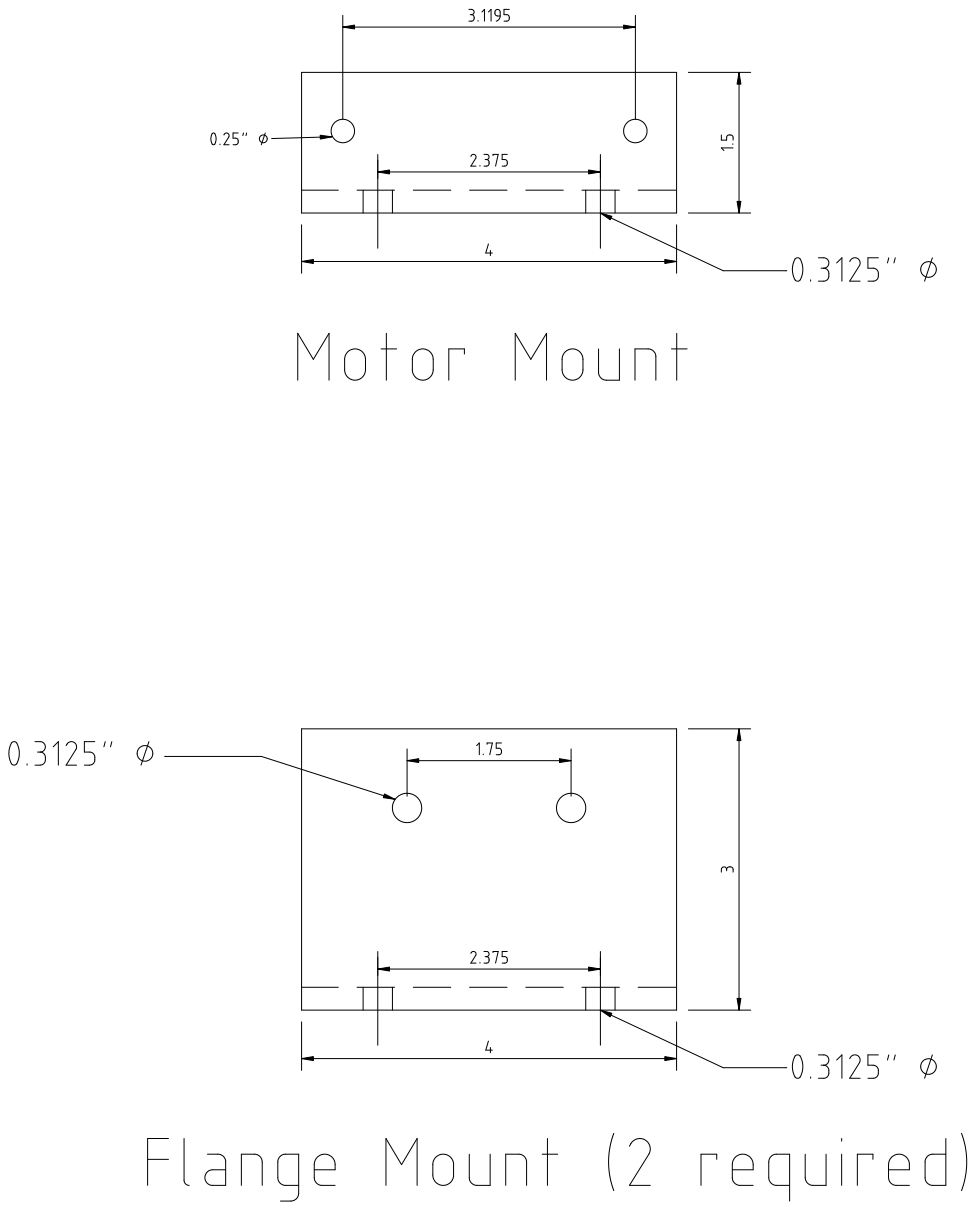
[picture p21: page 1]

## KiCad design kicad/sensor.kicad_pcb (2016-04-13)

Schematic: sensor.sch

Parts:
IC1: ATTINY45-S; SOIJ-8_5.3x5.3mm_Pitch1.27mm
O1: TSL1406R
P1: ICSP; Pin_Header_Angled_2x03
P2: LED; Pin_Header_Angled_1x02
R1: R100; R_1206
RV1: POT; Potentiometer_Trimmer-Piher-PT15-h2-5_vertical

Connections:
AO: IC1.2, O1.6, O1.12
CLK: IC1.3, O1.4, O1.10
GND: IC1.4, O1.1, O1.5, P1.6, RV1.3
MISO: IC1.6, O1.2, O1.3, O1.9, P1.1
MOSI: IC1.5, P1.4
unnamed: O1.7, O1.8
unnamed: P2.1, R1.1
unnamed: R1.2, RV1.2
RESET: IC1.1, P1.5
SCK: IC1.7, P1.3
VCC: IC1.8, O1.13, P1.2, P2.2

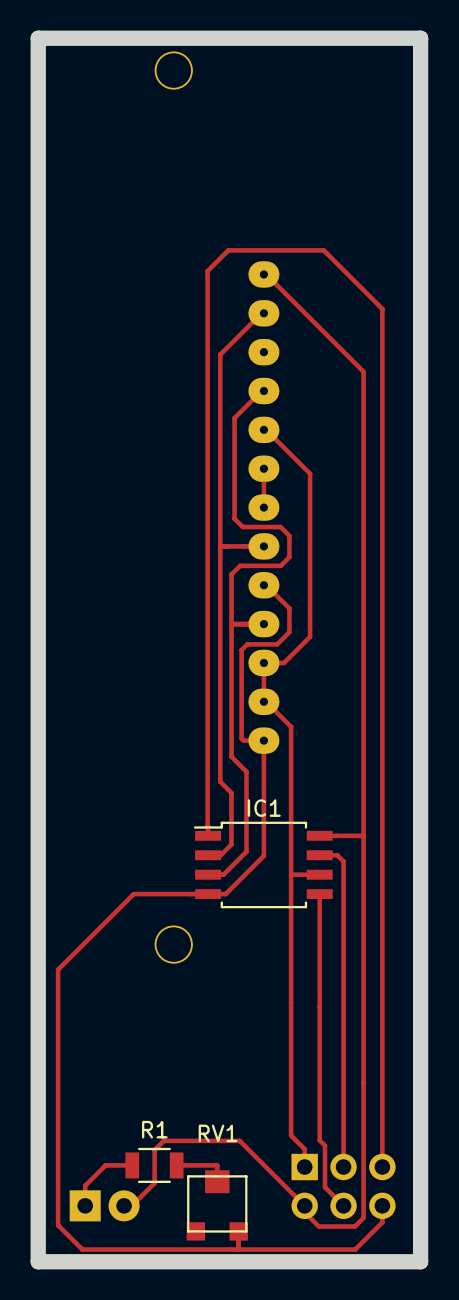
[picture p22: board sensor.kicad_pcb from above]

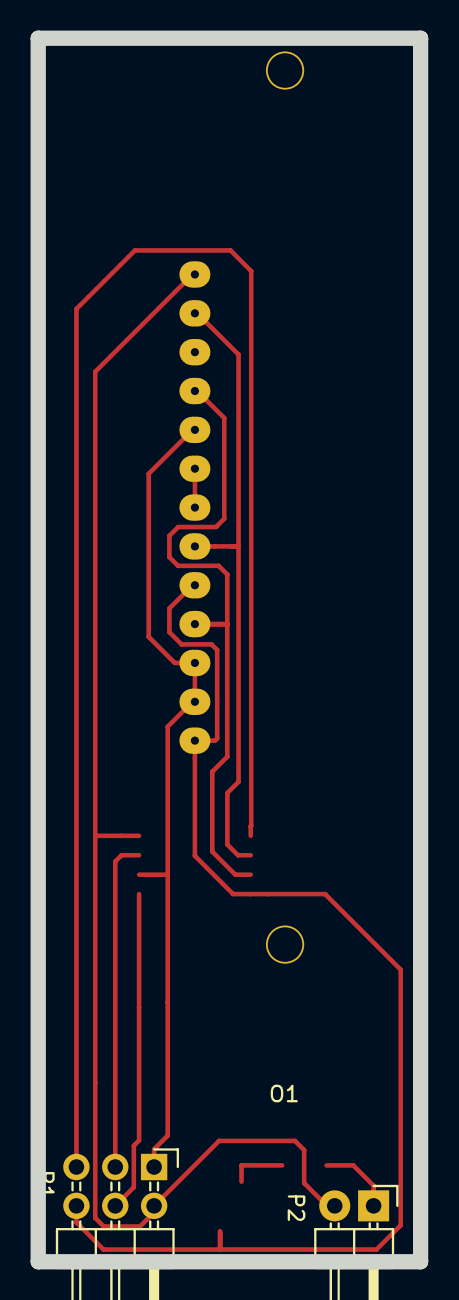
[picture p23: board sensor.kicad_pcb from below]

Board: 2 copper layers, 25.0 x 80.0 mm, 6 parts (3 on the bottom side), 11 nets.

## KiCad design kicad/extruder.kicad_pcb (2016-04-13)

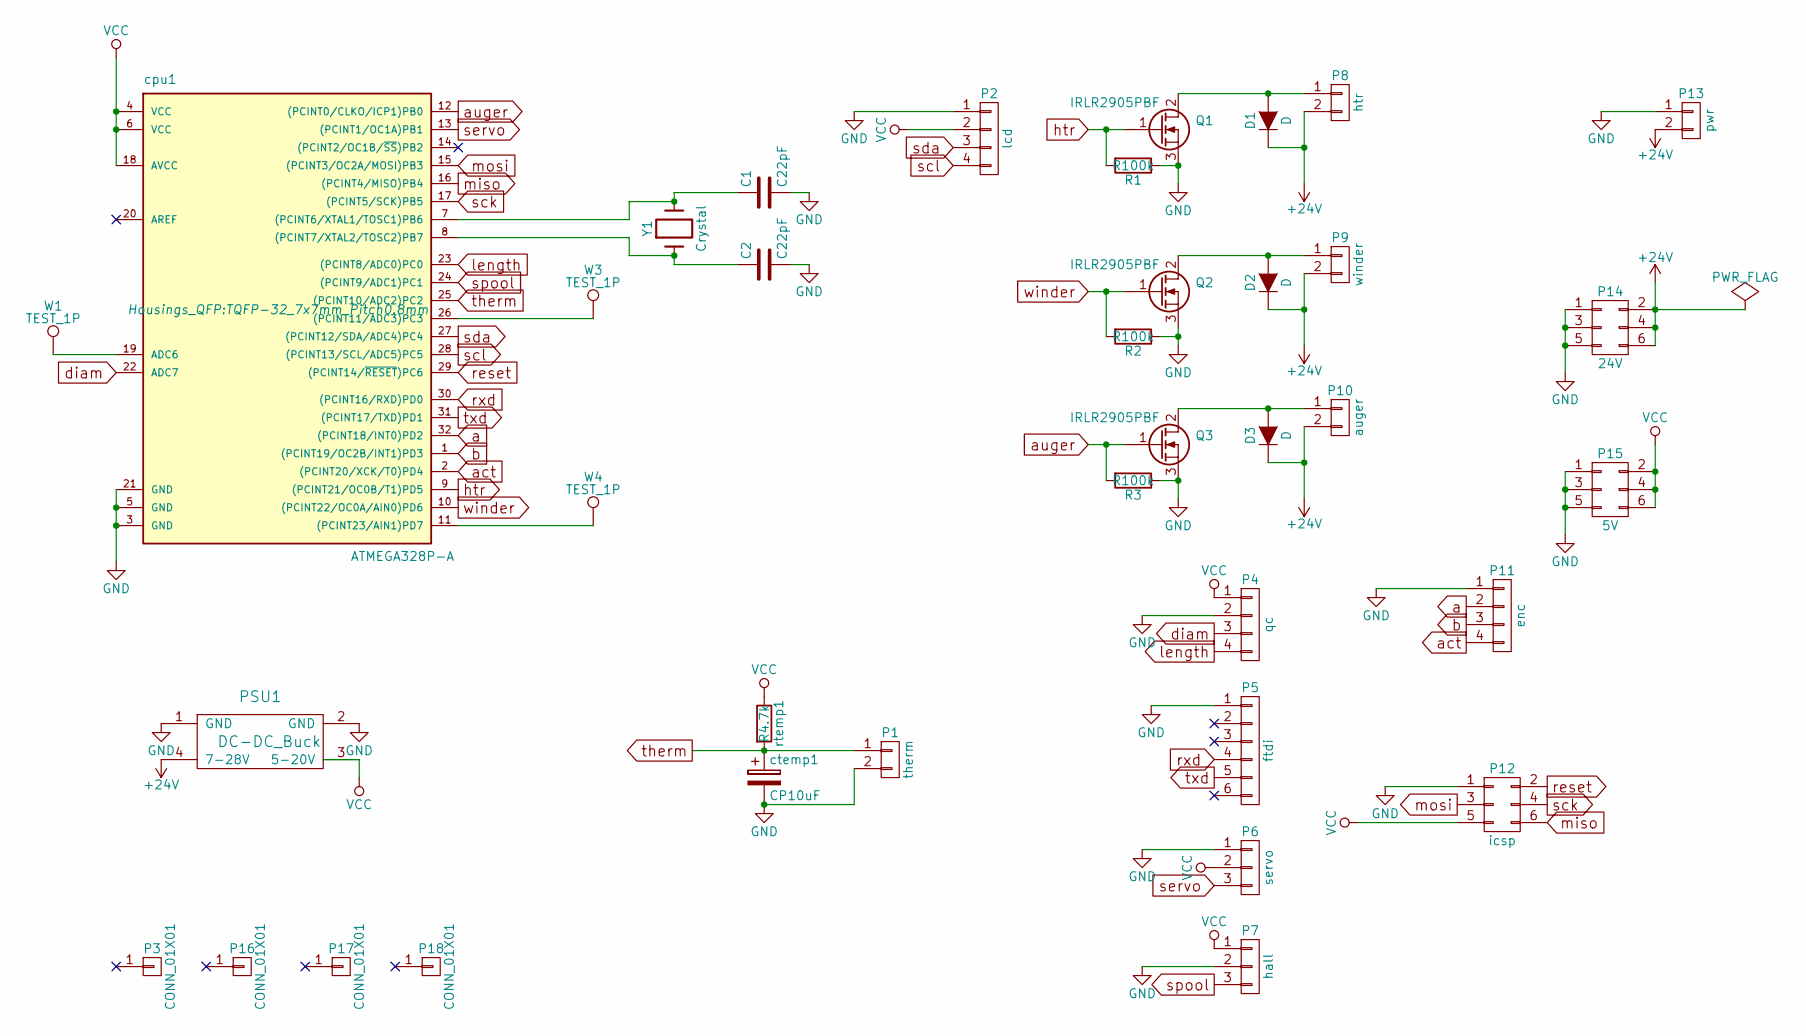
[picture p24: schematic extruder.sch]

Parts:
C1, C2: C22pF; C_0805
D1, D2, D3: D; DO-214AC
P1: therm; Pin_Header_Straight_1x02
P2: lcd; Pin_Header_Straight_1x04
P3, P16, P17, P18: CONN_01X01; 1pin
P4: qc; Pin_Header_Straight_1x04
P5: ftdi; Pin_Header_Straight_1x06
P6: servo; Pin_Header_Straight_1x03
P7: hall; Pin_Header_Straight_1x03
P8: htr; 2Screw
P9: winder; Pin_Header_Straight_1x02
P10: auger; 2Screw
P11: enc; Pin_Header_Straight_1x04
P12: icsp; Pin_Header_Straight_2x03
P13: pwr; 2Screw
P14: 24V; Pin_Header_Straight_2x03
P15: 5V; Pin_Header_Straight_2x03
PSU1: DC-DC_Buck; 7-28V
Q1, Q2, Q3: IRLR2905PBF; TO-252-2Lead
R1, R2, R3: R100k; R_0603
W1, W3, W4: TEST_1P; Pin_Header_Straight_1x01
Y1: Crystal; Crystal_HC49-SD_SMD
cpu1: ATMEGA328P-A; TQFP-32_7x7mm_Pitch0.8mm
ctemp1: CP10uF; c_elec_3x5.3
rtemp1: R4.7k; R_1206

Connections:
+24V: D1.1 (K), D2.1 (K), D3.1 (K), P8.2, P9.2, P10.2, P13.2, P14.2, P14.4, P14.6, PSU1.4 (7-28V)
GND: C1.2, C2.2, P1.2, P2.1, P4.2, P5.1, P6.1, P7.2, P11.1, P12.1, P13.1, P14.1, P14.3, P14.5, P15.1, P15.3, P15.5, PSU1.1 (GND), PSU1.2 (GND), Q1.3 (S), Q2.3 (S), Q3.3 (S), R1.1, R2.1, R3.1, cpu1.3 (GND), cpu1.5 (GND), cpu1.21 (GND), ctemp1.2
unnamed: C1.1, Y1.2, cpu1.7 ((PCINT6/XTAL1/TOSC1)PB6)
unnamed: C2.1, Y1.1, cpu1.8 ((PCINT7/XTAL2/TOSC2)PB7)
unnamed: D1.2 (A), P8.1, Q1.2 (D)
unnamed: D2.2 (A), P9.1, Q2.2 (D)
unnamed: D3.2 (A), P10.1, Q3.2 (D)
unnamed: W1.1, cpu1.19 (ADC6)
unnamed: W3.1, cpu1.26 ((PCINT11/ADC3)PC3)
unnamed: W4.1, cpu1.11 ((PCINT23/AIN1)PD7)
VCC: P2.2, P4.1, P6.2, P7.1, P12.5, P15.2, P15.4, P15.6, PSU1.3 (5-20V), cpu1.4 (VCC), cpu1.6 (VCC), cpu1.18 (AVCC), rtemp1.1
a: P11.2, cpu1.32 ((PCINT18/INT0)PD2)
act: P11.4, cpu1.2 ((PCINT20/XCK/T0)PD4)
auger: Q3.1 (G), R3.2, cpu1.12 ((PCINT0/CLKO/ICP1)PB0)
b: P11.3, cpu1.1 ((PCINT19/OC2B/INT1)PD3)
diam: P4.3, cpu1.22 (ADC7)
htr: Q1.1 (G), R1.2, cpu1.9 ((PCINT21/OC0B/T1)PD5)
length: P4.4, cpu1.23 ((PCINT8/ADC0)PC0)
miso: P12.6, cpu1.16 ((PCINT4/MISO)PB4)
mosi: P12.3, cpu1.15 ((PCINT3/OC2A/MOSI)PB3)
reset: P12.2, cpu1.29 ((PCINT14/~RESET~)PC6)
rxd: P5.4, cpu1.30 ((PCINT16/RXD)PD0)
sck: P12.4, cpu1.17 ((PCINT5/SCK)PB5)
scl: P2.4, cpu1.28 ((PCINT13/SCL/ADC5)PC5)
sda: P2.3, cpu1.27 ((PCINT12/SDA/ADC4)PC4)
servo: P6.3, cpu1.13 ((PCINT1/OC1A)PB1)
spool: P7.3, cpu1.24 ((PCINT9/ADC1)PC1)
therm: P1.1, cpu1.25 ((PCINT10/ADC2)PC2), ctemp1.1, rtemp1.2
txd: P5.5, cpu1.31 ((PCINT17/TXD)PD1)
winder: Q2.1 (G), R2.2, cpu1.10 ((PCINT22/OC0A/AIN0)PD6)

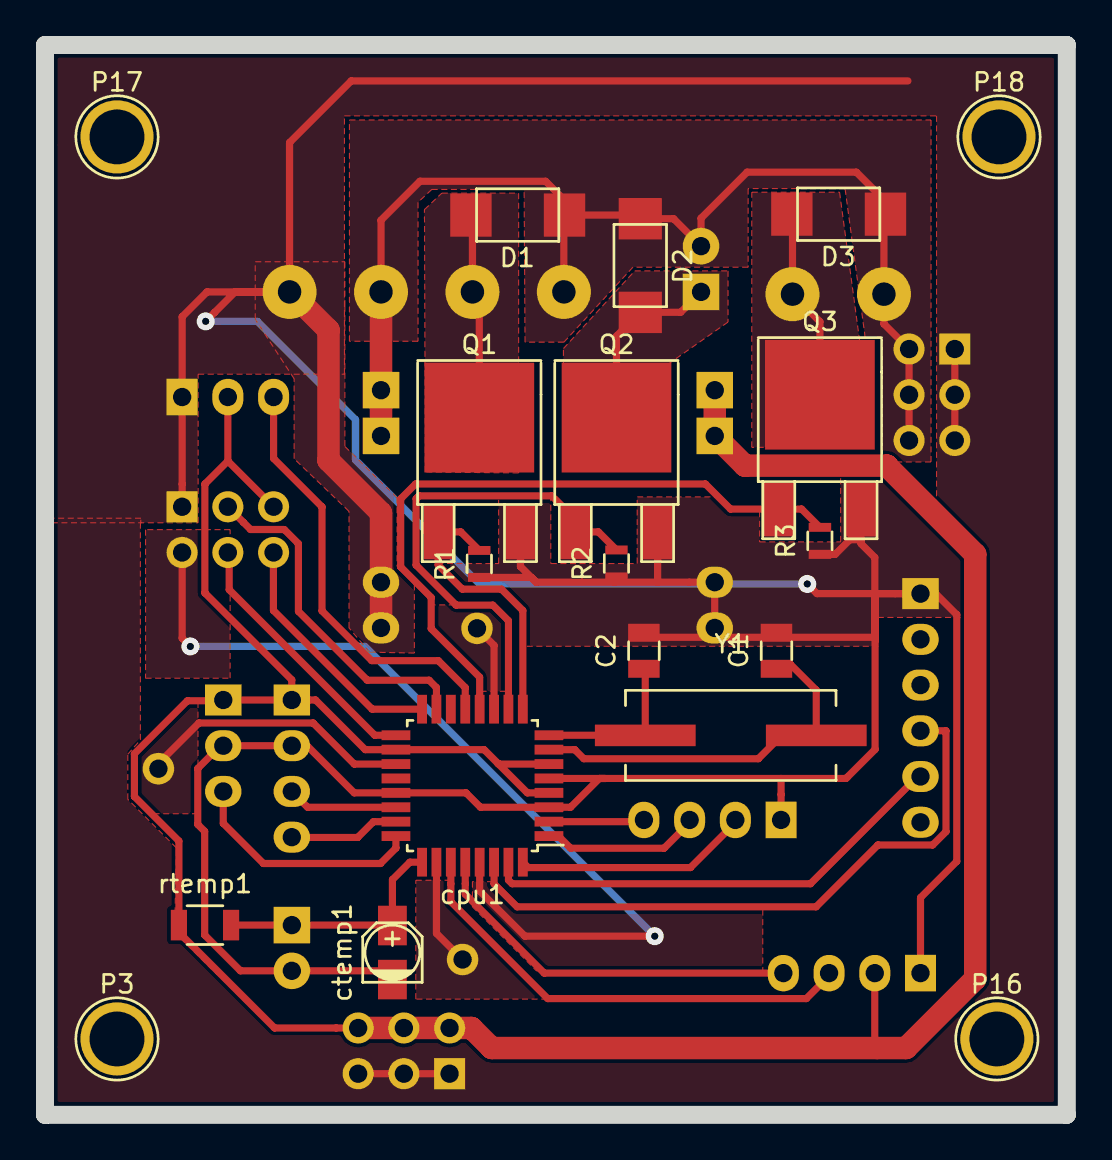
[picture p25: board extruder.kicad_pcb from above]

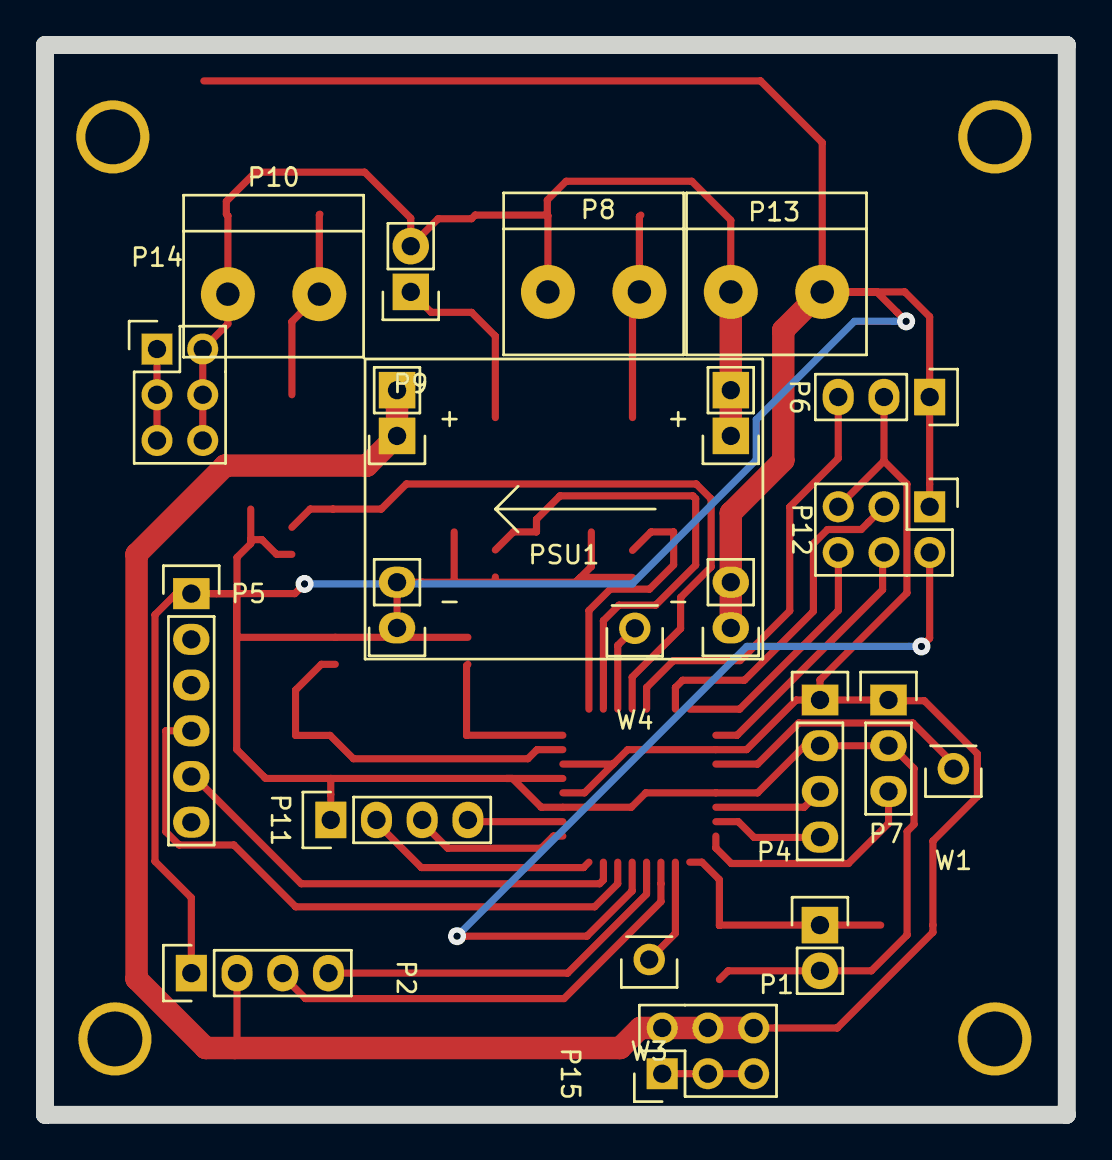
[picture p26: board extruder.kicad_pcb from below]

Board: 2 copper layers, 56.8 x 59.4 mm, 37 parts (18 on the bottom side), 30 nets.

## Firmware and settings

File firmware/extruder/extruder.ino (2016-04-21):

// vim: set foldmethod=marker filetype=cpp :
// Copyright 2015 Michigan Technological University {{{
// Based upon work by Ian Johnson (http://www.thingiverse.com/thing:174383)
// Author: Jerry Anzalone and Bas Wijnen
// This design was developed as part of a project with
// the Michigan Tech Open Sustainability Technology Research Group
// http://www.appropedia.org/Category:MOST
// It is released under CC-BY-3.0
// If you do not have a copy of the license, it may be found at: http://creativecommons.org/licenses/by/3.0/legalcode
// }}}

/*{{{*********  CONTROL LOGIC  **********

Controls are a rotary encoder with push button and a 16x2 lcd display.

At startup, the system is in auto mode.

Pressing the button enters the main menu.  Menu structure:

Main
	Manual Winder Speed -> Button to exit menu.
	Temperature
		Set target
		Set PID constants/auto-calibrate
	Filament Guide
		Set left
		Set right
		Set # steps
	QC
		Set calibration constants
	Back


}}} */

#define dbg(msg, data) do { Serial.print(msg); Serial.println(data); } while (0)
//#define SERIAL_LCD	// Enable LCD output to serial port.
//#define DEBUG_SENSOR	// Sensor data to serial port.
//#define FILAWINDER	// Use filawinder board.

uint8_t checkButton(bool block);

// Includes. {{{
#include <EEPROM.h>
#include <Arduino.h>
//#include <Servo.h> 
#include "PID_v1.h"
#include <LcdMenu.h>
#include <LiquidCrystal_I2C.h>
#include <Wire.h>
// }}}

/* Filawinder pin markings: {{{
0	rx		serial		+
1	tx		serial		+
2	auto +		UI A/B		+
3	guide min +	UI B/A		+
4	sensor cal +	UI Select	+
5	winder FET	Winder FET	+
6	servo		Servo		+
7	hall (H side)	Winder hall	#
8	guide max +	buzzer		x
9	h8				-
10	spi/h8		spi		+
11	spi/h8		spi		+
12	spi/h8		spi		+
13	spi/h8		spi		+
A0	sensor(20k)	heater FET	+
A1	sensor(20k)	auger FET	+
A2	sensor(20k)	QC length hall	#
A3	sensor(20k)	QC diameter	#
A4	i2c		i2c sda		+
A5	i2c		i2c scl		+
A6	knob				-
A7	h6		temperature	+
+-------------+
|  a0  a1  a2 |
| gnd vcc  a3 |
+----     ----+

icsp: key towards avr.
}}} */

/* Conversion between pin change interrupt numbers, port+pin pairs and arduino pin numbers: {{{
pcint	avr	pin		used as
00	B0	8		-				auger FET (this pin and/or 7)
01	B1	9		oc1a: winder FET
02	B2	10	spi ss	oc1b: guide servo		Cannot be used; is SS.
03	B3	11		spi mosi: icsp
04	B4	12		spi miso: icsp
05	B5	13		spi sck: icsp
06	B6			xtal1
07	B7			xtal2

08	C0	A0		c0: QC distance
09	C1	A1		c1: hall effect sensor
10	C2	A2		a2: temperature input
11	C3	A3		c3: buzzer
12	C4	A4		i2c sda: display
13	C5	A5		i2c scl: display
14	C6			reset: icsp
15	n/a	n/a

16	D0	0		uart rxd: serial
17	D1	1		uart txd: serial
18	D2	2		pcint18: ui a
19	D3	3		pcint19: ui b
20	D4	4		pcint20: ui select
21	D5	5		oc0b: auger FET			guide servo
22	D6	6		oc0a: heater FET
23	D7	7		-				auger FET (this pin and/or 8)

		A6		-
		A7		QC: diameter

}}} */

/*{{{************ Hardware connections. ************/
#ifdef FILAWINDER
// {{{
	// UI.
#define PIN_A		3
#define PIN_B		2
#define PC_PORT_NAME PIND
#define PC_CONTROL_BIT	2
#define PC_PORT_VECT PCINT2_vect
#define PIN_A_MASK	0x08
#define PIN_B_MASK	0x04
#define PIN_BUTTON	4
#define PIN_BUTTON_MASK	0x10
	// Heater.
#define PIN_TEMP	A7
#define PIN_HEATER	A0
// Define this as ! to invert the signal.
#define INVERT_HEATER !
	// Winder.
#define PIN_WINDER	5
#define PIN_HALL	7
#define PIN_GUIDE 	6
	// Auger motor.
#define PIN_AUGER	A1
// Define this as ! to invert the signal.
#define INVERT_AUGER !
	// QC.
#define PIN_LEN		A2
#define PIN_DIA		A3

// Spare: 8, 9, A6
// }}}
#else
// {{{
	// UI.
#define PIN_A		2
#define PIN_B		3
#define PC_PORT_NAME PIND
#define PC_CONTROL_BIT	2
#define PC_PORT_VECT PCINT2_vect
#define PIN_A_MASK	0x04
#define PIN_B_MASK	0x08
#define PIN_BUTTON	4
#define PIN_BUTTON_MASK	0x10
	// Heater.
#define PIN_TEMP	A2
#define PIN_HEATER	5
// Define this as ! to invert the signal.
#define INVERT_HEATER
	// Winder.
#define PIN_WINDER	6
#define PIN_HALL	A1
#define PIN_GUIDE 	9
	// Auger motor.
#define PIN_AUGER	8
// Define this as ! to invert the signal.
#define INVERT_AUGER
	// QC.
#define PIN_LEN		A3
#define PIN_DIA		A7

// Spare: 7, A3, A6
// }}}
#endif
// Sensor is on SPI: 10, 11, 12, 13.
// 10,11,12,13: SPI
// A4,A5: I2C
// 0,1: UART
// }}}

/************ Globals. ******************/
// UI. {{{
static bool send_status = true;
#define EEPROM_MAGIC 0x5a	// Content of EEPROM[0] to signify valid contents.
LiquidCrystal_I2C lcd(0x27, 16, 2);
#define debounce_time 10	// milliseconds.
#define knob_debounce_time 100	// milliseconds.
#define reset_time 1000	// time to hold button for lcd to reset in milliseconds.
static int *edit_num_target = NULL;
static volatile bool clicked;
static volatile int8_t delta;
static volatile unsigned long reset_start_time;
// }}}
// Heater. {{{
static uint8_t heater_phase, heater_duty;
static unsigned long last_temp_update;
static float heater_output;
static int raw_temp;
static uint8_t force_heater = 0;
static int T_KP = 10;	// %
static int T_KI = 30;	// %
static int T_KD = 200;	// %
// These are used to limit the value of the I buffer.
#define T_OP_MIN 0.
#define T_OP_MAX 100.
#define T_SAMPLE_TIME 1000  //ms
static double T_sp = 160, T_ip, T_op = 50;
static PID T_PID(&T_ip, &T_op, &T_sp, T_KP, T_KI / 1000., T_KD, DIRECT);
#ifdef THERMOCOUPLE
#define TEMP_A 1
#define TEMP_B 0
#else
#define ADCBITS 10
#define R0 10e3
#define R1 INFINITY
#define Rc 100e3
#define Tc (25 + 273.15)
float beta = 4420;
#define K (exp(log(Rc) - beta / Tc))
#endif
// }}}
// Winder. {{{
static int hall_state = HIGH;
static int last_hall_state = HIGH;
// Set these values based on the servo you are using.
#define GUIDE_PERIOD (1. / 50)
#define GUIDE_MIN_TIME 1e-3
#define GUIDE_MAX_TIME 3e-3
// These values should never change.
#define PRESCALE 8
#define GUIDE_TICK_TIME (PRESCALE * 1. / F_CPU)
#define GUIDE_TICKS_PER_PERIOD (uint16_t(GUIDE_PERIOD / GUIDE_TICK_TIME + .5))
#define GUIDE_MIN_TICKS (uint16_t(GUIDE_MIN_TIME / GUIDE_TICK_TIME + .5))
#define GUIDE_MAX_TICKS (uint16_t(GUIDE_MAX_TIME / GUIDE_TICK_TIME + .5))
static double guide_min = -49;		// guide limiting positions.
static double guide_max = -21;
static int guide_direction = 1;		// direction  changes upon reaching min or max
static double guide_current;		// current guide position
static int guide_steps = 40;		// the number of increments for the guide to cover the range.
static volatile uint8_t sensor = 0;
static volatile uint8_t pixels;
static uint8_t last_pixel = 0;
#define CONST 1
// }}}
// Auger motor. {{{
#define MIN_TEMP 130
#define MAX_TEMP 300
static bool auger_on = false;
static int8_t force_winder = 0;	// -1 is auto, 0 is off, 1 is max.
// }}}
// QC. {{{
static float diameter = 0;
static float dia_slope = -514.12;
static float dia_intercept = 1267.58;
static int len_hall_state = HIGH;
static int last_len_hall_state = HIGH;
static float total_length = 0;
static float len_step = .0355;
static unsigned long last_report;	// For limiting QC output to serial.
// }}}

/*************** Functions. *****************/
// Winder. {{{
static volatile uint8_t sensor_state = 0;
static volatile uint8_t sensor_sync_phase = 1;
#ifdef DEBUG_SENSOR
#define SENSOR_DATA_LEN 20
static volatile uint8_t sensor_data[SENSOR_DATA_LEN];
static volatile uint8_t sensor_state_data[SENSOR_DATA_LEN];
static volatile uint8_t sensor_data_pos = 0;
#endif
ISR(SPI_STC_vect) { // {{{
	uint8_t data = SPDR;
#ifdef DEBUG_SENSOR
	if (sensor_data_pos < SENSOR_DATA_LEN) {
		sensor_data[sensor_data_pos] = data;
		sensor_state_data[sensor_data_pos++] = sensor_state;
	}
#endif
	if (sensor_state == 0) {
		pixels = data;
		sensor_state = 1;
	}
	else if (sensor_state == 1) {
		sensor = data;
		sensor_state = 2;
	}
	else {
		if (sensor_sync_phase == 0)
			sensor_sync_phase = data != 0x53;
		sensor_state = 1;
	}
} // }}}

static void sync_sensor() { // {{{
	static int8_t wait = 0;
	switch(sensor_sync_phase) {
	case 0:
		return;
	case 1:
		digitalWrite(PIN_HEATER, INVERT_HEATER(false));
		digitalWrite(PIN_AUGER, INVERT_AUGER(false));
		Serial.println("Syncing sensor");
		lcd.clear();
		lcd.print("Syncing sensor");
		pinMode(SCK, INPUT);
		sensor_sync_phase = 2;
		pixels = 0;
		wait = 10;
		// Fall through.
	case 2:
		if (pixels == 0) {
			wait -= 1;
			if (wait > 0)
				return;
			Serial.println("Sensor syncing");
			wait = 10;
			pinMode(MISO, OUTPUT);
			digitalWrite(MISO, LOW);
			SPCR = 0x00;
			delay(100);
#ifdef DEBUG_SENSOR
			//sensor_data_pos = 0;
#endif
			sensor_state = 0;
			SPCR = 0xe0;
			pinMode(MISO, INPUT);
			return;
		}
		// Sync completed.
		sensor_sync_phase = 0;
		Serial.print("Sensor synchronized: ");
		Serial.println(pixels);
	}
} // }}}

static uint8_t handle_winder() { // {{{
	sync_sensor();
	if (sensor_sync_phase)
		return 0;
#ifdef DEBUG_SENSOR // {{{
	if (true) {
		cli();
		uint8_t len = sensor_data_pos;
		Serial.print("sensor data:");
		for (uint8_t i = 0; i < len; ++i) {
			Serial.print(" ");
			Serial.print(sensor_data[i]);
		}
		Serial.print("\nsensor state:");
		for (uint8_t i = 0; i < len; ++i) {
			Serial.print(" ");
			Serial.print(sensor_state_data[i]);
		}
		Serial.print("\n");
		sensor_data_pos -= len;
		sei();
	}
#endif // }}}
	if (force_winder >= 0) {
		return force_winder * 255;
	}
	uint8_t pixel = sensor;
	if (pixel > 0 && pixel < pixels - 1)
		last_pixel = pixel;
	//dbg("sensor: ", pixel);
	float pos = ((last_pixel * 1.0 / pixels - .5) * 2 * CONST) / 2 + .5; // range 0-1
	//dbg("measure ", pos);
	if (pos <= 0)
		return 0;
	else if (pos >= 1)
		return 255;
	else
		return 255 * pos;
} // }}}

static void set_guide(double angle) { // {{{
	uint16_t value = (angle + 90) * (GUIDE_MAX_TICKS - GUIDE_MIN_TICKS) / 180 + GUIDE_MIN_TICKS;
	OCR1AH = value >> 8;
	OCR1AL = value & 0xff;
} // }}}

static void handle_guide() { // {{{
	if (edit_num_target) {
		return;
	}
	hall_state = digitalRead(PIN_HALL);
	if (hall_state == LOW && hall_state != last_hall_state) {
		last_hall_state = hall_state;
		// it just switched to high, calculate what to do with the guide
		// the calculation of position is entirely dependent upon the position of the filament in the guide
		// but the filament runs through a slot, so it could be anywhere.
		// provide means for adjusting increment on the fly.
		guide_current += guide_direction * 1.0 * (guide_max - guide_min) / guide_steps;
		if (guide_current >= guide_max) {
			guide_direction = -1;
			guide_current = guide_max;
		}
		if (guide_current <= guide_min) {
			guide_direction = 1;
			guide_current = guide_min;
		}
		set_guide(guide_current);
	}
	else
		last_hall_state = hall_state;
} // }}}
// }}}
// UI. {{{
extern uint8_t const PROGMEM chars[8][8] = {
	{0x1f, 0x1f, 0x1f, 0x1f, 0x1f, 0x1f, 0x1f, 0x1f},	// heat off, auger off, auger not requested.
	{0x02, 0x07, 0x07, 0x07, 0x06, 0x00, 0x0c, 0x0c},	// heat off, auger off, auger requested. (ALARM!)
	//{0x00, 0x00, 0x00, 0x00, 0x00, 0x00, 0x00, 0x00},	// heat off, auger on, auger not requested (doesn't happen).
	{0x1f, 0x1f, 0x1f, 0x1f, 0x1f, 0x1f, 0x1f, 0x1f},	// Instead use a copy of char 0, because it is treated as end of string.
	{0x00, 0x00, 0x00, 0x04, 0x04, 0x15, 0x0e, 0x04},	// heat off, auger on, auger requested.
	{0x11, 0x11, 0x1f, 0x1f, 0x1f, 0x1f, 0x1f, 0x1f},	// heat on, auger off, auger not requested.
	{0x11, 0x11, 0x1f, 0x1b, 0x1b, 0x0a, 0x11, 0x1b},	// heat on, auger off, auger requested.
	{0x00, 0x00, 0x00, 0x00, 0x00, 0x00, 0x00, 0x00},	// heat on, auger on, auger not requested (doesn't happen).
	{0x0e, 0x0e, 0x00, 0x04, 0x04, 0x15, 0x0e, 0x04}};	// heat on, auger on, auger requested.
static void init_lcd() { // {{{
	lcd.init();
	lcd.backlight();
	lcd.clear();
	for (uint8_t i = 0; i < 8; ++i) {
		uint8_t data[8];
		for (uint8_t b = 0; b < 8; ++b)
			data[b] = pgm_read_byte(&chars[i][b]);
		lcd.load_custom_character(i, data);
	}
	//lcd_reset = false;
} // }}}

ISR(PC_PORT_VECT) {	// {{{
	static bool a, b;
	uint8_t data = PC_PORT_NAME;
	bool new_a = data & PIN_A_MASK;
	bool new_b = data & PIN_B_MASK;
	bool new_select = !(data & PIN_BUTTON_MASK);
	if (!new_select) {
		reset_start_time = millis();
	}
	else if (millis() - reset_start_time > debounce_time)
		clicked = true;
	if (a != new_a) {
		delta += new_a ^ new_b ? 1 : -1;
	}
	if (b != new_b) {
		delta += new_a ^ new_b ? -1 : 1;
	}
	a = new_a;
	b = new_b;
} // }}}
uint8_t checkButton(bool block) {	// {{{
	static unsigned long idle_time;
	uint8_t ret = 0;
	cli();
	if (clicked) {
		ret |= BUTTON_SELECT;
		clicked = false;
	}
	if (delta >= 4) {
		ret |= BUTTON_DOWN;
		delta -= 4;
		idle_time = millis();
	}
	else if (delta <= -4) {
		ret |= BUTTON_UP;
		delta += 4;
		idle_time = millis();
	}
	else if (idle_time + knob_debounce_time > millis())
		delta = 0;
	sei();
	return ret;
} // }}}
static uint8_t edit_num(int &target, char const *msg, int min, int max, bool digit) {	// {{{
	if (edit_num_target != &target) {
		edit_num_target = &target;
		message(msg, "");
		lcd.setCursor(0, 1);
		if (digit) {
			if (target < 0)
				lcd.print("-");
			lcd.print(abs(target) / 10);
			lcd.print(".");
			lcd.print(abs(target) % 10);
		}
		else
			lcd.print(target);
		lcd.print("      ");
#ifdef SERIAL_LCD
		Serial.println(target);
#endif
	}
	uint8_t button = checkButton(false);
	if (button & BUTTON_DOWN && target < max) {
		target += 1;
		lcd.setCursor(0, 1);
		if (digit) {
			if (target < 0)
				lcd.print("-");
			lcd.print(abs(target) / 10);
			lcd.print(".");
			lcd.print(abs(target) % 10);
		}
		else
			lcd.print(target);
		lcd.print("      ");
#ifdef SERIAL_LCD
		Serial.println(target);
#endif
	}
	if (button & BUTTON_UP && target > min) {
		target -= 1;
		lcd.setCursor(0, 1);
		if (digit) {
			if (target < 0)
				lcd.print("-");
			lcd.print(abs(target) / 10);
			lcd.print(".");
			lcd.print(abs(target) % 10);
		}
		else
			lcd.print(target);
		lcd.print("      ");
#ifdef SERIAL_LCD
		Serial.println(target);
#endif
	}
	if (button & BUTTON_SELECT) {
		edit_num_target = NULL;
		return 0;
	}
	return WAIT;
} // }}}
MenuItem(back) {	// {{{
	return BACK;
} // }}}

// Startup Menu. {{{
MenuItem(toggle_winder) {	// {{{
	force_winder = !force_winder;
	return 0;
} // }}}
MenuItem(toggle_heater) {	// {{{
	force_heater = !force_heater;
	return 0;
} // }}}
MenuItem(toggle_auger) {	// {{{
	auger_on = !auger_on;
	return 0;
} // }}}
MenuItem(startup_back) {	// {{{
	if (force_winder)
		force_winder = -1;
	return BACK;
} // }}}
static Menu <4> startup_menu(	"Startup" , (char const *[]){"Toggle Heater", "Toggle Winder", "Toggle Auger", "Back"}, (action *[]){&toggle_heater, &toggle_winder, &toggle_auger, &startup_back});
//				"........#170.5°C"
// }}}

// Heater Menu. {{{
MenuItem(temp_set) {	// {{{
	static int T;
	if (!edit_num_target) {
		T = T_sp;
	}
	uint8_t ret = edit_num(T, "Set temp target", 0, 500, false);
	T_sp = T;
	return ret;
} // }}}
MenuItem(pid_p) {	// {{{
	int ret = edit_num(T_KP, "Proportional(%/K)", 0, 200, false);
	T_PID.SetTunings(T_KP, T_KI / 1000., T_KD);
	return ret;
} // }}}
MenuItem(pid_i) {	// {{{
	int ret = edit_num(T_KI, "I(.01%/Ks)", 0, 200, true);
	T_PID.SetTunings(T_KP, T_KI / 1000., T_KD);
	return ret;
} // }}}
MenuItem(pid_d) {	// {{{
	int ret = edit_num(T_KD, "Derivative(s%/K)", 0, 1000, false);
	T_PID.SetTunings(T_KP, T_KI / 1000., T_KD);
	return ret;
} // }}}
static Menu <4> pid_menu(	"PID"     , (char const *[]){"Proportional", "Integration", "Derivative", "Back"}, (action *[]){&pid_p, &pid_i, &pid_d, &back});
static Menu <3> temp_menu(	"Heater"  , (char const *[]){"Set Target", "Set PID", "Back"}, (action *[]){&temp_set, &pid_menu, &back});
//				"........#170.5°C"
// }}}

// Guide Menu. {{{
MenuItem(guide_set_min) {	// {{{
	guide_current = guide_min;
	int setting = guide_current;
	uint8_t ret = edit_num(setting, "Set Min Guide", -90, 90, false);
	guide_min = setting;
	guide_current = setting;
	set_guide(guide_current);
	return ret;
} // }}}
MenuItem(guide_set_max) {	// {{{
	guide_current = guide_max;
	int setting = guide_current;
	uint8_t ret = edit_num(setting, "Set Max Guide", -90, 90, false);
	guide_max = setting;
	guide_current = setting;
	set_guide(guide_current);
	return ret;
} // }}}
MenuItem(guide_set_steps) {	// {{{
	return edit_num(guide_steps, "Set Guide Steps", 0, 255, false);
} // }}}
static Menu <4> guide_menu(	"Guide"     , (char const *[]){"Set Right", "Set Left", "Set # of Steps", "Back"}, (action *[]){&guide_set_min, &guide_set_max, &guide_set_steps, &back});
// }}}

// QC Menu. {{{
MenuItem(qc_report) {	// {{{
	if (checkButton(false) & BUTTON_SELECT)
		return 0;
	lcd.setCursor(0, 0);
	lcd.print("Diameter:");
	lcd.print(diameter);
	lcd.print("mm     ");
	lcd.setCursor(0, 1);
	lcd.print("Length:");
	lcd.print(total_length);
	lcd.print("m     ");
	return WAIT;
} // }}}
#if 0
MenuItem(qc_dia_slope) {	// {{{
	return edit_num(dia_slope, "Dia Slope", -1000, 1000, true);
} // }}}
MenuItem(qc_dia_intercept) {	// {{{
	return edit_num(dia_intercept, "Dia Intercept", -10000, 10000, true);
} // }}}
MenuItem(qc_len_step) {	// {{{
	return edit_num(len_step, "Length Step", 0, 1000, true);
} // }}}
static Menu <5> qc_menu(	"QC"      , (char const *[]){"Report", "Dia Slope", "Dia Intercept", "Length Step", "Back"}, (action *[]){&qc_report, &qc_dia_slope, &qc_dia_intercept, &qc_len_step, &back});
//				"........#170.5°C"
#endif
// }}}

template <typename T> void save_item(int &addr, T const &item) {	// {{{
	for (unsigned int i = 0; i < sizeof(T); ++i)
		EEPROM.write(addr++, (reinterpret_cast <char const *>(&item))[i]);
} // }}}
template <typename T> void load_item(int &addr, T &item) {	// {{{
	union {
		char data[sizeof(T)];
		T result;
	} convert;
	for (unsigned int i = 0; i < sizeof(T); ++i)
		convert.data[i] = EEPROM.read(addr++);
	item = convert.result;
} // }}}
MenuItem(save) {	// {{{
	int addr = 0;
	EEPROM.write(addr++, EEPROM_MAGIC);	// Magic marker to detect valid data.
	save_item(addr, auger_on);
	save_item(addr, T_KP);
	save_item(addr, T_KI);
	save_item(addr, T_KD);
	save_item(addr, beta);
	save_item(addr, T_sp);
	save_item(addr, guide_min);
	save_item(addr, guide_max);
	save_item(addr, guide_steps);
	save_item(addr, dia_slope);
	save_item(addr, dia_intercept);
	save_item(addr, len_step);
	return BACK;
} // }}}
static void load() { // {{{
	int addr = 0;
	int magic = EEPROM.read(addr++);
	if (magic != EEPROM_MAGIC) {
		Serial.print("Magic doesn't match; not loading settings (");
		Serial.print(magic, 16);
		Serial.println(")");
		return;
	}
	load_item(addr, auger_on);
	load_item(addr, T_KP);
	load_item(addr, T_KI);
	load_item(addr, T_KD);
	load_item(addr, beta);
	load_item(addr, T_sp);
	load_item(addr, guide_min);
	load_item(addr, guide_max);
	load_item(addr, guide_steps);
	load_item(addr, dia_slope);
	load_item(addr, dia_intercept);
	load_item(addr, len_step);
} // }}}
static Menu <5> main_menu(	""        , (char const *[]){"Startup", "Heater", "Guide", "QC", "Save"}, (action *[]){&startup_menu, &temp_menu, &guide_menu, &qc_report, &save});
//				"........#170.5°C"
// }}}
// Heater. {{{
static float current_temp;

static float read_temp() {
	raw_temp = analogRead(PIN_TEMP);
#ifdef THERMOCOUPLE
	raw_temp * TEMP_A + TEMP_B;
#else
	return -beta / log(K * ((1 << ADCBITS) / R0 / raw_temp - 1 / R0 - 1 / R1)) - 273.15;
#endif
}
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
void loop() { // {{{
	current_temp = read_temp();
	bool run_auger = auger_on && current_temp >= MIN_TEMP && current_temp < MAX_TEMP;
	char buffer[15];
	uint8_t pos = 0;
	char indicator = ((force_heater && T_op > 0.) << 2) | ((run_auger) << 1) | ((auger_on) << 0);
	buffer[pos++] = indicator ? indicator : 2;	// Use otherwise unused character 2 to avoid triggering end of string.
	if (current_temp < 0)
		buffer[pos++] = '-';
	pos += snprintf(buffer + pos, sizeof(buffer) - pos - 1, "%d.", int(abs(current_temp)));
	buffer[pos++] = '0' + int(abs(current_temp) * 10) % 10;
	pos += snprintf(buffer + pos, sizeof(buffer) - pos - 1, "/%d", int(T_sp));
	buffer[pos++] = 0;
	// UI.
	unsigned long now = millis();
	main_menu.iteration(false, buffer);
	// Heater.
	T_ip = current_temp;
	if (!force_heater) {
		heater_duty = 0;
		digitalWrite(PIN_HEATER, INVERT_HEATER(false));
	}
	else if (T_PID.Compute()) {
		//dbg("pid out: ", T_op);
		heater_output = T_op;
		if (heater_output <= 0)
			heater_output = 0;
		else if (heater_output >= 100)
			heater_output = 100;
		heater_duty = heater_output;
	}
	if (now - last_temp_update >= 100) {
		// Manual pwm of heater.
		digitalWrite(PIN_HEATER, INVERT_HEATER(heater_duty > heater_phase));
		heater_phase += 1;
		heater_phase %= 100;
		while (now - last_temp_update >= 100)
			last_temp_update += 100;
	}
	// Winder.
	analogWrite(PIN_WINDER, handle_winder());
	handle_guide();
	// Auger motor.
	digitalWrite(PIN_AUGER, INVERT_AUGER(run_auger));
	// QC.
	update_len();
	// Report once per second.
	if (!sensor_sync_phase && now - last_report >= 1000) {
		diameter = (analogRead(PIN_DIA) - dia_intercept) / dia_slope;
		if (send_status) {
			Serial.print(total_length);
			Serial.print("\t");
			Serial.print(diameter);
			Serial.print("\t");
			Serial.print(current_temp);
			Serial.print("\t");
			Serial.print(raw_temp);
			Serial.print("\t");
			Serial.print(T_op);
			Serial.print("\t");
			Serial.print(T_PID.GetITerm());
			Serial.print("\n");
		}
		while (now - last_report >= 1000)
			last_report += 1000;
	}
	handle_serial();
} // }}}

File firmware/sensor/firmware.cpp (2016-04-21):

// Firmware for the attiny in the sensor.
/*
   Communication protocol:
   Sensor is bus master; host is slave.
   SS is not used.  Instead, MISO is pulled low by host to initiate reset.
   After reset, sensor sends number of used pixels and enters main loop.
   During main loop with DEBUG_MODE set, every pixel is sent to the host.
   During main loop without DEBUG_MODE set, the position of the shadow is sent for every frame, followed by 0x53.
   If the host does not receive 0x53, it requests a reset.
 */

#include <avr/io.h>
#include <avr/interrupt.h>
#include <math.h>

// Hardware:
// IC connections:
// 1: reset			b5	i
// 2: sensor ao		adc3	b3	i
// 3: sensor clk		b4	o
// 4: gnd
// 5: mosi			b0	o
// 6: miso/sensor si		b1	o
// 7: sck			b2	o
// 8: vcc

#define HWPIXELS 768
#define SKIP 81	// On both sides.
#define EACHBITS 5
#define EACHMASK ((1 << EACHBITS) - 1)
#define VALID_LIMIT 100	// Maximum value for min_ao to still be valid.
#define PIXELS ((HWPIXELS - 2 * SKIP) >> EACHBITS)
#define DELAY 100
#define SHORT_DELAY 5

// Uncomment the next line to send maximum pixel instead of index of lowest.
//#define SEND_MAX

#define CLK_PIN 4
#define SI_PIN 1
#define DO_PIN 0
#define SCK_PIN 2

#define ddrb 0x15	// output for bits 0, (1), 2, 4.
#define adcsra 0x80	// Enable ADC, prescaler 2. (should be 8 for full range.)

static inline void delay(uint32_t time) {
	for (uint32_t i = 0; i < time; ++i)
		asm volatile ("nop");
}

static void send_data(uint8_t pos) {
	for (uint8_t i = 0; i < 8; ++i) {
		if ((pos >> i) & 1) {
			PORTB = 1 << DO_PIN;
			PORTB = (1 << DO_PIN) | (1 << SCK_PIN);
			delay(SHORT_DELAY);
			PORTB = 1 << DO_PIN;
			delay(SHORT_DELAY);
		}
		else {
			PORTB = 0;
			PORTB = 1 << SCK_PIN;
			delay(SHORT_DELAY);
			PORTB = 0;
			delay(SHORT_DELAY);
		}
	}
}

// While changing si, all other pins are always 0.
static void set_si() {
	DDRB = ddrb;	// SI input.
	PORTB = 1 << SI_PIN; // with pullup.
}

static void pulse() {
	int portb = PORTB;
	PORTB = portb | (1 << CLK_PIN);
	PORTB = portb;
}

static void clear_si() {
	PORTB = 0;	// No pullup.
	DDRB = ddrb | (1 << SI_PIN);	// output.
}

volatile int8_t state = 0;
volatile int8_t current = 0xff;
volatile int16_t sum;

// States:
// 0: normal measument.
// 1: normal; seen at least one measurement.
// bit 6: first reading after sync; ignore.
// bit 7: wait for sync.

ISR(TIMER1_COMPA_vect) {
	if (state & 0x80)
		return;
	set_si();
	pulse();
	if (!(PINB & (1 << SI_PIN))) {
		state |= 0xc0;
		// Synchronize; wait for the pin to return to high.
		while (!(PINB & (1 << SI_PIN))) {}
		// Finish reading.
		pulse();
		clear_si();
		for (int i = 0; i < HWPIXELS; ++i)
			pulse();
		// Send sensor length.
		send_data(PIXELS & 0xff);
		state &= ~0x80;	// Leave 0x40 set, so the first reading is ignored.
		TIFR = 1 << OCF1A;
		return;
	}
	clear_si();
	int idx = 0, min_idx = -1;
	int min_ao = 0x100;
	int i = 0;
	sum = 0;
#ifdef SEND_MAX
	int max_ao = -1;
#endif
	for (; i < SKIP; ++i)
		pulse();
	for (; i < HWPIXELS - SKIP; ++i) {
		if ((i & EACHMASK) == 0) {
			ADCSRA = adcsra | (1 << ADSC);
			while (ADCSRA & (1 << ADSC)) {}
			int ao = ADCH & 0xff;
#ifdef SEND_MAX
			if (ao > max_ao)
				max_ao = ao;
#endif
			sum += ao;
#ifndef DEBUG_MODE
			if (ao < min_ao) {
				min_ao = ao;
				min_idx = idx;
			}
#else
			send_data(ao);
#endif
			idx += 1;
		}
		pulse();
	}
	for (; i < HWPIXELS; ++i)
		pulse();
	if (state == 0) {
#ifdef SEND_MAX
		current = max_ao;
#else
		if (min_ao < VALID_LIMIT)
			current = min_idx;
#endif
		state = 1;
	}
	else
		state &= ~0x40;
}

static inline void set_state(uint8_t s) {
	cli();
	state = (state & ~0x2f) | s;
	sei();
}

int main() {
	// Set up the pins.
	PORTB = 0;
	DDRB = ddrb;
	// Set up the ADC.
	ADCSRA = adcsra;
	ADCSRB = 0x00;
	ADMUX = 0x23;
	DIDR0 = 1 << ADC3D;
	// Set up the clock.
	TCCR1 = 0xcf;	// PWM, 2 full overflows per second.
	OCR1A = 1;
	OCR1C = DELAY;	// More overflows per second.
	GTCCR = 0;
	TIFR = 1 << OCF1A;
	TIMSK = 1 << OCIE1A;
	sei();
	while(1) {
#ifndef DEBUG_MODE
		set_state(0);
		while (state != 1) {}
		send_data(current);
		send_data(0x53);
#endif
	}
}

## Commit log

2016-02-25 added kicad
    [extruder.kicad_pcb, extruder.sch]
2016-03-16 updated schematic
    [extruder.kicad_pcb, extruder.sch]
2016-04-05 updated scads
    [filament_winder.scad, filament_winder_renderer.scad]
2016-04-05 new sensor mount
    [filament_winder.scad, filament_winder_renderer.scad]
2016-04-12 fixed bom
    [filament_extruder_BOM.ods]
2016-04-13 updated electronics
    [extruder.kicad_pcb, extruder.sch]
2016-04-13 added sensor board
    [sensor.kicad_pcb, sensor.sch]
2016-04-13 added cad
    [filament_extruder.scad, filament_winder.scad, filament_winder_renderer.scad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]
2016-04-13 updated scad and fixed renderings again
    [filament_extruder.scad, filament_extruder_renderer.scad, filament_winder.scad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]
2016-04-13 added stl modles
    [bearing_bushing.stl, display_mount.stl, encoder_knob.stl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]
2016-04-14 added gerbers
    [extruder-B.CrtYd.gbr, extruder-B.Cu.gbr, extruder-B.Fab.gbr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]
2016-04-15 updated scad
    [filament_extruder.scad, filament_extruder_renderer.scad]
2016-04-15 updated feed chute
    [feed_chute_back.stl, feed_chute_front.stl]
2016-04-15 updated BOM for new feed chute
    [filament_extruder_BOM.ods]
2016-04-18 added electronics BOMs
    [extruder.csv, sensor.csv]
2016-04-21 add sensor-spy
